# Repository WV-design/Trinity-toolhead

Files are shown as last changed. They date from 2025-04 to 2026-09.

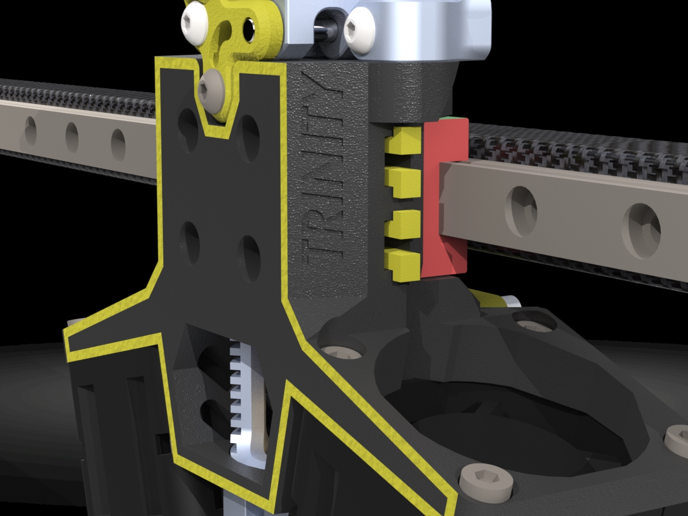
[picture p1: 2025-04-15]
renders/Untitled Project (17).jpg

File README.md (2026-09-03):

# __Trinity-toolhead__

Taking inspiration from Takeoff, Calamity, Tiger's toolhead, IROB and fiberstream, I came up with this: 
A small footprint unibody high performance toolhead.

Untitled Project (5)

> [!NOTE]  
> This is currently being tested, I am still working on it and would love your feedback!
> This project lives in a user project in the monolith discord server.

* Made to DUEL! the Y footprint fits within a sherpa mini so it takes up very little space in a dual gantry printer.
* Double 3628 fans deliver enough cooling even for hot chambers.
* The hotend is braced at the bottom of the heatsink to increase stiffness and decrease deflection.
* Balanced center of mass (COM) for lower rail wear and deflection.
* Single piece body to maximize stiffness and minimize weight.

## Compatibility:

> [!WARNING]  
> This toolhead is still in ACTIVE development! There may be newer CAD on the monolith discord server, the files on this github page are a stable release but miss features.

<!--
### Voron
Partial compatibility with voron trident and voron 2 gantries 
* Gantry must be flipped
* Cablechains for X cant be used
-->

### Monolith
Compatible with gates gt2 (and epdm) 6 and 9mm belts mgn12

## BOM:

| Amount | part | Note |
|-|-|-|
| 1 | Hotend | Recommended: <br /> [dragon ace volcano](https://trianglelab.net/products/dragon-ace%E2%84%A2-hotend?VariantsId=11350) |
| 1 | Extruder | Recommended: <br /> [Sherpa mini](https://www.fysetc.com/products/cnc-all-metal-sherpa-v3-extruder-light-weight-kit-36-moons) |
| 2 | 3628 fan | Recommended: <br /> [Delta FFB03612EHNYCL](https://www.digikey.com/en/products/detail/delta-electronics/FFB03612EHNYCL/6580720)|
| 1 | 2510 fan | Recommended: <br /> [delta ASB02505SHA-AY6B](https://www.digikey.com/en/products/detail/delta-electronics/ASB02505SHA-AY6B/7491489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) |
| 1 | SLM monolith belt clamp | https://monolith-gantry-updates.zen3d.eu/monolith-slm-belt-clamps/ |
| 4 | part cooling fan mounting | m3x35mm socket head | 
| 2 | part cooling fan mounting | m3x35 button head (these can be replaced with 2 more socket head screws)|
| 1 | K face mounting bolt | m3x30 button head|
| 4 | rail mounting bolts | m3x20 socket head|
| 2 | extruder mounting bolt | m3x12 button head|
| 11 | heat set insert | m3x4/5mm |
| 4 | hotend mounting bolts | m2.5x8mm | 
| 2 | hotend fan mounting | m2.5x12mm | 
| 2 | square nut | DIN 557 m3  |

## Print Settings:
* Layer heights
  - body: <= 0.2mm
  - ducts: ideally ~0.1mm to make them smoother but anything from 0.1-0.24 should work
  - apex clips: ~0.1mm so the different thicknesses print properly
  - belt clamp plate ideally <= 0.12mm to get the teeth to interface with the belt better 
* Wall count: => 5
* Top/bottom layers: => 6
* Infill: shouldnt really matter because of the walls and top layers but => 20% is nice for printing. My recommendation: 40% multi wall triangle infil 
* Print the parts **slowly**, strength and layer adhesion are important for the toolhead's performance. To achieve this, you can simply limit the flowrate in your slicer.
  
### material choice:
> [!NOTE]  
> * Fiber filled filaments are preferred because of the increase in stiffness.
> * The apex clips should NOT be printed in a brittle material or be annealed! They can snap when inserting but will be fine once in place.
* < 70C ABS 
* < 100C PC-PBT/PET (NOT PETG!) (annealed)
* PC (look for a Tg of ~130C or higher, the rest is blended/impure and may creep)
* PPS (annealed) (also what chamber temp are you planning to go for?? poor fans...)

> [!IMPORTANT]  
> make sure the ends of your belts are in good condition. If you re-use belts that have been used in another toolhead, be sure to double check them. This belt is a good example of a damaged one, the teeth are crushed so they wont grip the toolhead as well. <br />
 <br />
> You need to check what belt clips fit best, this can differ per printer. You should use the **thickest** belt clamp that can still be inserted with one finger, friction is good but you dont want to damage the belt. There is a clip size test available in the "extras" folder. Also make sure the clips are in **all the way**. If the belts are not seated well the clips may not go in all the way. Below here are 2 examples of improperly installed clips. Make sure the legs of the clips are perfectly **parallel** and that all clips sit at the same height. <br /><br />



## Credits
Thanks to:
Prooda, I'd consider him a co-designer at this point. He gave me lots of feedback and spent long nights refining the design.
Martin, he's done a *lot* of work on modding trinity!

Apex, for your [awesome belt clips](https://github.com/ApexArray/ApexClips) and the insight!

Wayne, for the [monolith belt clamps](https://github.com/CloakedWayne/MISC/tree/main/Monolith_SLM_belt_clamps)

Hartk, for the [voron construct repository!](https://github.com/PrintersForAnts/Voron-Construct)

DK and Adeo, on the insights on the ducts!

Barthini and Caza for early feedback on the design

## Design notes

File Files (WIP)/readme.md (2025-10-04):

### Heads up, read this page before printing!
- Trinity is too tall for most belt tensioners, therefore Prooda developed a new one. This can be found in the "extras" section
- Want to use a toolhead board ~~To increase the y footprint~~ ? Check out the "extras" section, the files are made for the "xol toolboard" and the "Mellow fly sht36 v2".
- Want probe mounts? Beacon works natively and buckshot/klicky00 (with an adapter plate in... you guessed it "Extras"!)

### selection single/multi color (from version 1.42 on)
I designed a "logo cutout" piece so you can choose how to print the logo. Options include:



- multi color. the file includes inset edges on the front face, so the slicer should be able to easily fill the faces with colors. [You can do this on a normal single toolhead printer without an mmu if you change the filament by hand](https://www.youtube.com/watch?v=6m_Wf59O1xk)
  


- single color with inset logo, for this option you need to do some slicer tricks. You can use one of the "logo cutouts" (outlines or the 3 shapes) as a negative body to cut into the main body.  It's explained in [this video](https://www.youtube.com/watch?v=_e7CY2rMzgA)

- single color without logo, this is the easiest (and a bit lame if you ask me), you simply delete the logo cutouts before printing.

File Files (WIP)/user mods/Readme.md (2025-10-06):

## Welcome to the usermods page. Thanks everyone for building, modding and upgrading trinity, I love to see the different variants pop up!
These projects are not my work so if you have questions you should contact the maker, feel free to do so in the trinity channel though!

### Prooda:
Made for the same configuration as trinity except with ["chube compact"](https://www.lukeslabonline.com/products/chube-compact), this version of trinity is basically its own cad now because everything was changed. Ask prooda if you have questions about this version.
supports mgn9 with 6mm belts, and mgn12 with 6 & 9mm belts. NOTE that the ducts are wider than the original trinity ducts

### Zerodegree79
Added support for the ["magneto filament cutter"](https://biqu.equipment/products/bigtreetech-magneto-cutter-auto-loading-magnetic-filament-cutter-for-vzbot-3d-printer-toolhead-high-precision-upgrade-accessories) Designed to be used with the [A4T - WWBMG - Dual sensor Sherpa-Mini spacing](https://github.com/Armchair-Heavy-Industries/A4T/blob/main/CAD/WW-BMG%20for%20A4T/A4T%20-%20WWBMG%20-%20Main_Body%20%5BSherpa-Mini%20spacing%5D%20Dual%20Sensor.step)
- The chube compact version is almost untouched from prooda's design
- the volcano UHF and t-volcano(NOT ACE) versions include a hotend fan duct based on tas' work with a4t, include a thermistor for the heatsink, and uses square nuts to mount the extruder.
- 
Notes:
The ducts on the volcano versions are not compatible with the klicky mount because the third mounting point is removed, the ducts from prooda's version or the original trinity files are compatible though

### cpp0xc0ffeeee:
Added support for the ["mellow heatercore"](https://3dmellow.com/products/mellow-heatcore-4-uhf-alps-hotend-smart-leveling-nozzle-probe-for-voron-blv-vzbot-hevort-diy-3d-printer-high-flow-and-high-speed) hotend and monolith belt clips by Tas

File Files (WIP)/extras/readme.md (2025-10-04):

### READ BEFORE PRINTING
* The toolboard mounts have 2 mounting options, a normal one and a lowered one. The lowered mounting version is MGN9 only! They are designed for the "Mellow fly sht36 v2" and the xol toolboard but can be adapted to others by users. The reason for those toolboards is the support for tachometer wires for the fans, these are not required but they are nice. 
* The pre tensioner is made to work with 2020 extrusions, not aluminium or carbon tubes

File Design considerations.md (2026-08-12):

Hi! If you're here you probably want to learn more about the design and how/why it was made. I don't want to talk about those nerdy details in the readme so I made this!
If you have questions, feel free to reach out to me via discord!

### Form factor
This whole design started from wanting a toolhead with a super minimal Y footprint. I am working on a dual gantry printer where toolhead Y losses are doubled because there are well... 2 gantries. I didnt really find anything that had a super low Y footprint so I decided on a little scope creep as a treat. 

I am looking to go reasonably spicy with my printer's chamber (~80c) so I wanted good cooling, more on this in the *cooilng* section. I considered dual 5015 blower fans, but then I found tigers toolhead, takeoff, calamity and IROB, which all used 3628 axial fans to great effect. Then I had the idea of placing the hotend and fans under the X axis instead of in front like calamity does. This results in a toolhead that is super compact in the Y direction, and can balance the mass of the components very well. The result is a toolhead with extra travel in Y, great cooling, and a well placed center of mass (COM). It does, however result in significant Z loss because the toolhead is quite tall. 2 of these toolheads next to eachother take up a similar Y footprint compared to a stealthburner (with cable chain).




### cooling
As said before, 2 3628's were chosen for the task of cooling plastic below its glass transition temperature (Tg) as fast as possible. This is difficult because the chamber's temperature can be just a few degrees below the material's leading to poor heat exchange because of the low temperature delta. After looking around, I found that CBON's ducts were referenced a lot but they are meant more as area cooling ducts. They prioritize airflow over aiming the air, which is great for going very fast but I wanted to try something more focused. I took the challenge of simulating the ducts in CFD, one of the first things I noticed is that I needed to either:
* Make the ducts longer to give more space for the air direction to change, this idea is flawed because these axial fans dont have much static pressure. They don't like back pressure so the ducts needed to be unrestrictive.
or:
* rotate the fans slightly (this takes a bit of room in z but it allows me to make very short ducts. It also allows me to split up the airflow in an 'area cooling' and 'focused cooling' part. The great thing about the tilt is that the focused cooling has more length for the ducts to curve while simultaneously keeping the area cooling part short.


There are a few features that I think stand out:
* there is a cone coming from the hub of the fans to remove the area of lower pressure air behind the motor hub. This aims to lower turbulence and improve the flow rate a bit, but it also helps keep the ducts more rigid and printable. 
* The ducts themselves don't need any supports to be printed, and I am very proud of that. The probe mount options sadly may require supports. 

### Compatiblity
With the strict requirements of good COM, print-ability, stiffness, and keeping a low footprint, the task of adding compatibility gets exponentially more difficult. the toolhead body needs to change for every variant which adds up fast. Just having 6 and 9/10mm belt, mgn9 and 12 rail, and Sherpa mini and orbiter extruder support would mean I need to make 2*2*2=8 versions of the toolhead body. This gets unsustainable with slight changes or improving the CAD. At one point the project got so overwhelming that I did not want to touch it anymore so change was needed.
First, plans for supporting a filament cutter, or filament sensor were quickly scrapped. The same was done with the mgn9 rail variant, because monolith is designed for a mgn12 rail so thats what most users opt for. On top of that, the orbiter variants seemed to perform poorly with a double Y peak on the input shaper graphs. This likely meant that the extruder was "nodding" around the z axis despite the built in support for the motor that sticks out. Because of this, orbiter support was dropped.

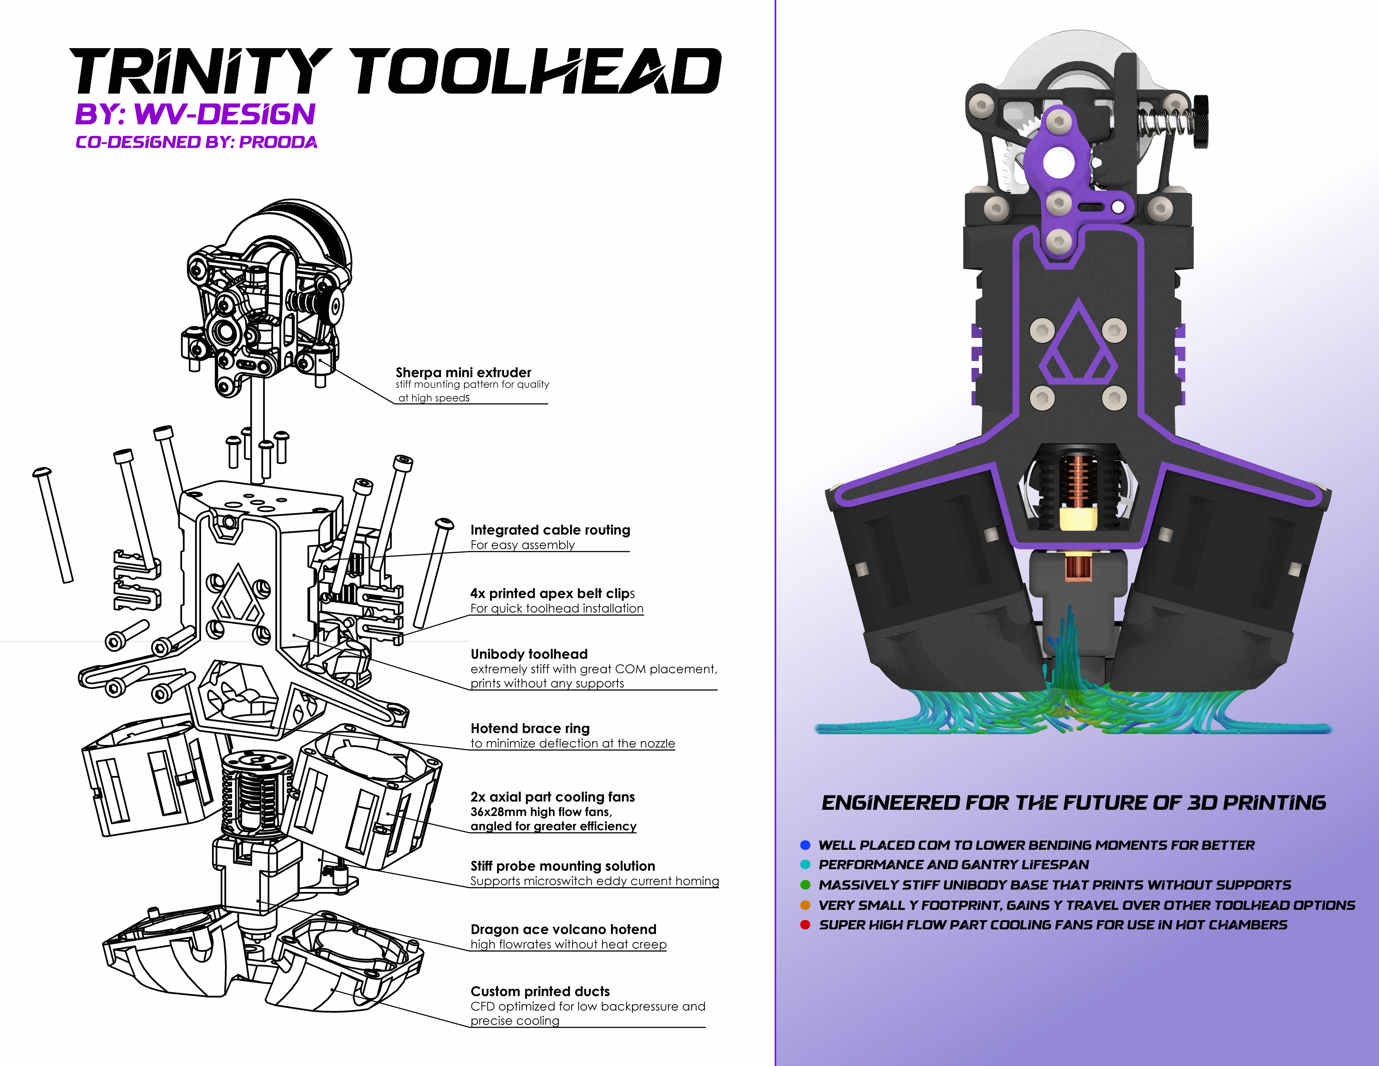
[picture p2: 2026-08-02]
renders/trinity toolhead poster.png

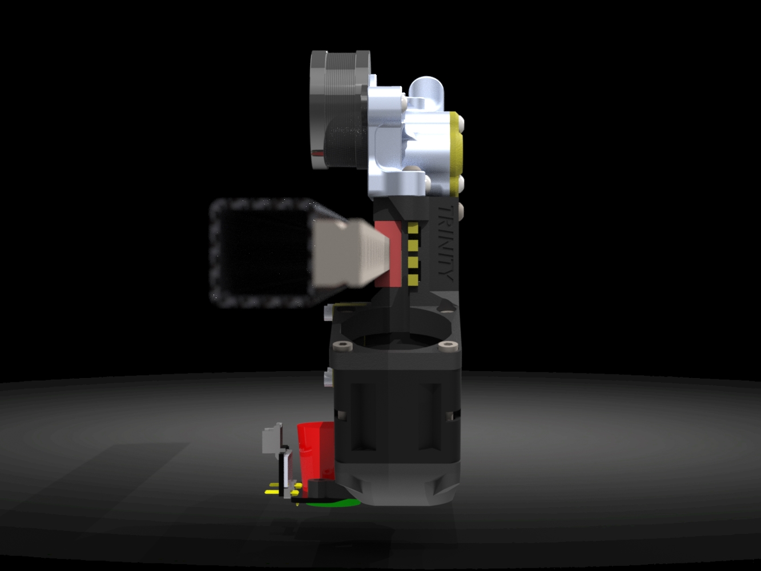
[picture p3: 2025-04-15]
renders/Untitled Project.jpg

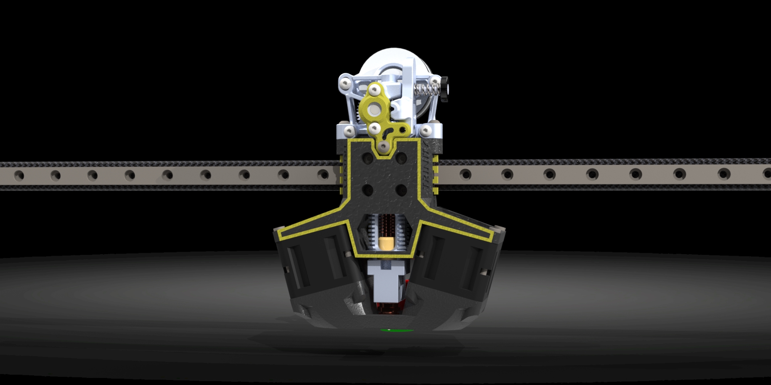
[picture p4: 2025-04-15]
renders/Untitled Project (16).jpg

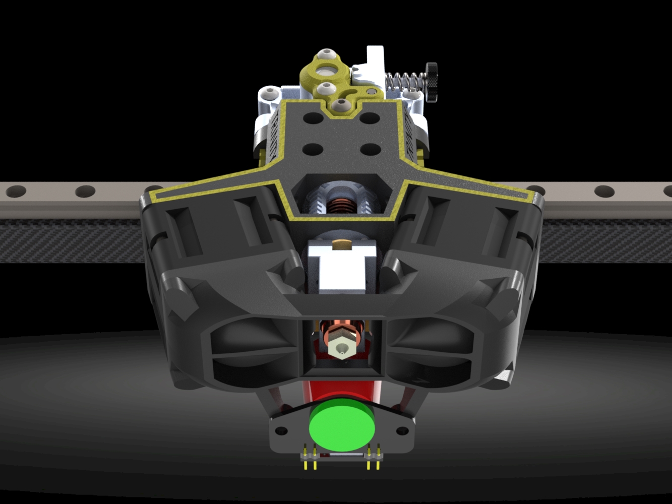
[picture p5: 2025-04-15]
renders/Untitled Project (18).jpg

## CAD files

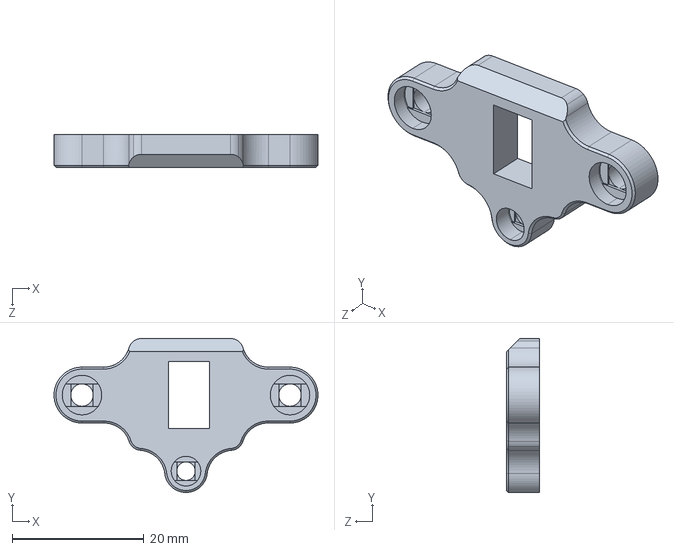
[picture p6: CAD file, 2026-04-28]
Files (WIP)/extras/Trinity klicky00 mounting plate by Prooda.STEP
40.1 x 23.4 x 5.00 mm

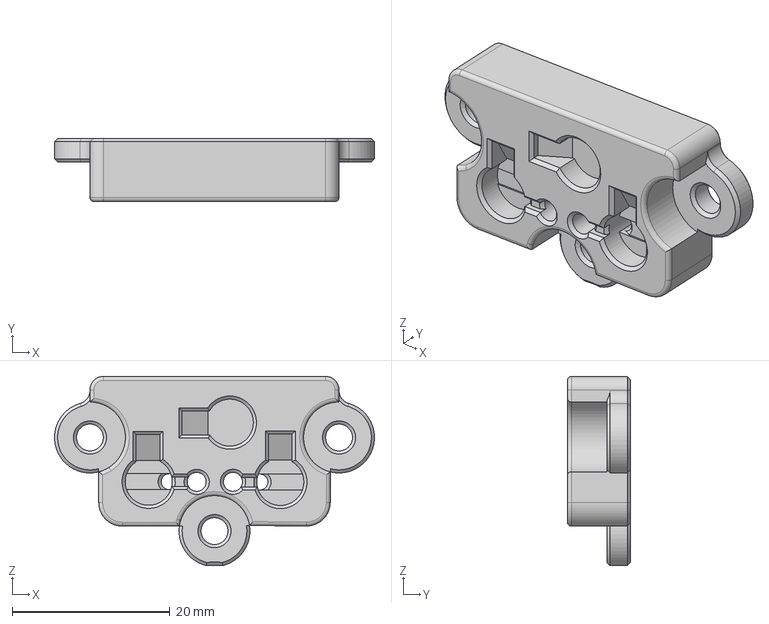
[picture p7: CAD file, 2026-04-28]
Files (WIP)/extras/HVFDesigns Trinity_Klicky_Mount.step
40.6 x 8.00 x 24.0 mm

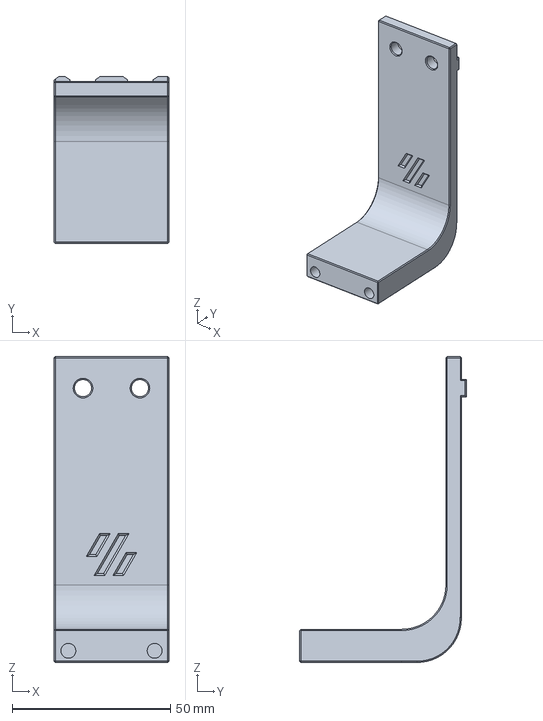
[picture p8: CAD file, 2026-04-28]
Files (WIP)/extras/HVFDesigns Trinity Klicky Dock Mount.step
36.3 x 52.8 x 96.7 mm

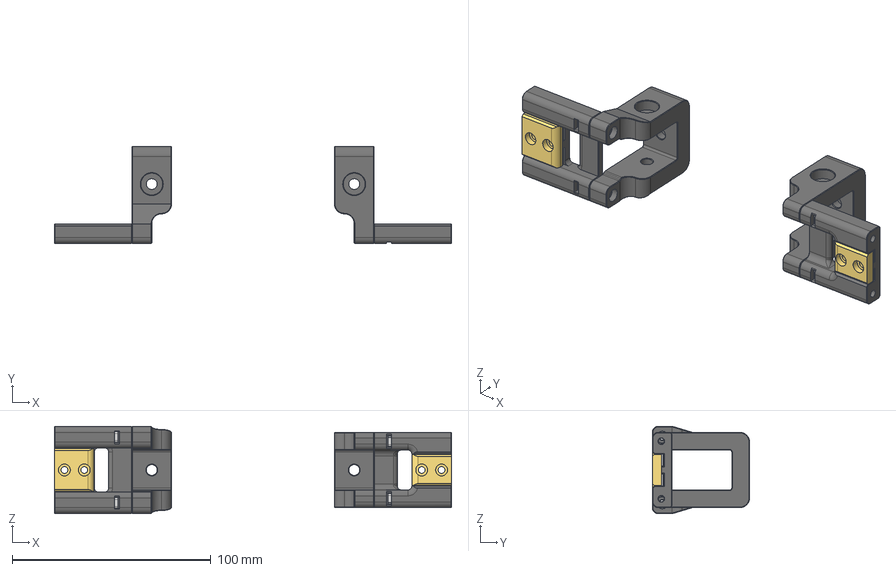
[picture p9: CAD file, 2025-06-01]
Files (WIP)/extras/Trinity pre tensioner by Prooda.step
200.0 x 49.0 x 44.0 mm
Pretensioner Belts Holder (1)
Pretensioner Belts Clamp (1)
Pretensioner Base (1)
M3 Square Nut x 2
Pretensioner Belts Holder (1)_1
Pretensioner Belts Clamp (1)_1
Pretensioner Base (1)_1
M3 Square Nut (1)
M3 Square Nut (1) (1)

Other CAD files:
Files (WIP)/extras/Trinity klicky mounting plate by Prooda.STEP

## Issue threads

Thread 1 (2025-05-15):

Source Files

5teveO, 2025-05-15:
Hi

I'm looking at adapting this toolhead to use on a self designed cross xy machine (I designed and built it for my 8 year old son) and was just wondering what it was you used to design it (fusion?) and if the source files were available for me to utilise so i can adjust the  mounting method etc.

Sorry for raising it as an issue - seems to be the only way to communicate on GH.

Steve

5teveO, 2025-05-15:
> Hi there!
>
> The project was made in Solidworks 2023, I dont mind sharing the source files with a few people but I plan to make them public when I have cleaned up the cad a little bit more.

Hi

Thanks for the quick response. No problem - I run fusion 360 so cant import solidworks anway.. so i'll just have to work with the step files and try and recreate the sections I need to modify. I'm really interested to see how it works and if it isnt so good on the crossxy, then i'm sure it will be good on my big slinger (470 cubed build area) as its quite a fast machine now, that needs lots of cooling!

Closed 2025-05-19.

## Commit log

2025-04-08 Create print instructions.md
2025-04-12 Update print instructions.md
2025-04-12 Create what to print.md
2025-04-23 I should go to bed
2025-05-15 Rename print instructions.md to readme.md
2025-06-01 Rename Files (WIP)/Trinity toolhead v1.4 mgn12 SLM clamp 6mm belts.step to Files (WIP)/toolheads/Trinity toolhead v1.4 mgn12 SLM clamp 6mm belts.step
    [Trinity toolhead v1.4 mgn12 SLM clamp 6mm belts.step]
2025-06-01 Rename Files (WIP)/6 & 9mm Pretensioners by Prooda.step to Files (WIP)/extras/6 & 9mm Pretensioner by Prooda.step
    [6 & 9mm Pretensioner by Prooda.step, 6 & 9mm Pretensioners by Prooda.step]
2025-06-01 Update and rename Files (WIP)/Trinity klicky mounting plate by Prooda.STEP to Files (WIP)/extras/Trinity klicky mounting plate by Prooda.STEP
    [Trinity klicky mounting plate by Prooda.STEP]
2025-06-01 Rename Files (WIP)/Trinity toolhead board mounts by Prooda.step to Files (WIP)/extras/Trinity toolhead board mounts by Prooda.step
    [Trinity toolhead board mounts by Prooda.step]
2025-06-01 Update and rename Files (WIP)/toolheads/Trinity toolhead v1.4 mgn12 SLM clamp 6mm belts.step to Files (WIP)/Trinity toolhead v1.4 mgn12 SLM clamp 6mm belts.step
    [Trinity toolhead v1.4 mgn12 SLM clamp 6mm belts.step]
2025-06-01 Update and rename Trinity toolhead v1.4 mgn12 SLM clamp 6mm belts.step to Trinity toolhead v1.4 mgn12 SLM clamp 6mm belts.step
    [Trinity toolhead v1.4 mgn12 SLM clamp 6mm belts.step]
2025-10-04 Rename Zerodegrees79 Chube Compact Trinity Magneto Cutter MGN12 6mm.zip to Zerodegree79 Chube Compact Trinity Magneto Cutter MGN12 6mm.zip
2026-04-28 Update and rename Trinity klicky mounting plate by Prooda.STEP to Trinity klicky00 mounting plate by Prooda.STEP
    [Trinity klicky00 mounting plate by Prooda.STEP]
